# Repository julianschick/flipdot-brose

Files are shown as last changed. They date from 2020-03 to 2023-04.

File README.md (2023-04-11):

# flipdot-brose
Leiterplattenlayout für die Ansteuerung von Brose-Flipdotmodulen.

## Teileliste

Mit passenden Artikelbezeichnungen für den Berliner Elektroteilehändler [Segor](https://www.segor.de).

Anzahl | Beschreibung | Segor-Artikelbezeichnung
--|--|--
2 | Hohlsteckerbuchse für Printmontage 2,1/5,5mm | *DCBU 2,1-PRNB*
3 | Miniatursicherungshalter Littelfuse RM 5,08mm | *RSI-Halter/LP*
3 | Rundsicherungen träge (1A, 4A, 5A) | *RSI 1,0 A T*; *RSI 4,0 A T*; *RSI 5,0 A T*
1 | JST VH-Buchse 3-polig 90° | *B3PS-VH*
1 | Diode mind. 2A und 30V | *1N 5062*
1 | Diode mind. 6A und 5V | *P 600 M*
1 | Keramikkondensator 100n RM 2,5mm | *u10-R2.5-X7R*
1 | Elektrolytkondensator 10u RM 2,5mm | *ELRA 10u-50/105°/6,3x7*
1 | Linearregler 3.3V min. 500mA Formfaktor TO220 | *LD 1117 V33* 
6 | Shift-Register 8Bit 74HC595 | *74HC 595 N*
1 | Octal-Transceiver 76HC245 | *74HC 245 N*
4 | NPN-Darlington-Array 8 Bit ULN2803A | *ULN 2803 A*
2 | High-Side-Driver TD62783 (oder UDN2981) | *TD62783 APG*
8 | Widerstand 10K RM 5,08mm |
1 | ESP32-Development-Board NodeMCU/DEVKITV1 (15 Pole je Reihe und VCC- und GND-Pin nebeneinander)
1 | Wannenstecker 60-polig (2x30) RM 2,54mm mit (oder ohne) Niederhalter
1 | Pinheader 10-polig (2x5) RM 2,54mm (und passende Kurzschlussbrücken dazu)
2 | Pinheader 16-polig RM 2,54mm (eigentlich 15-polig)

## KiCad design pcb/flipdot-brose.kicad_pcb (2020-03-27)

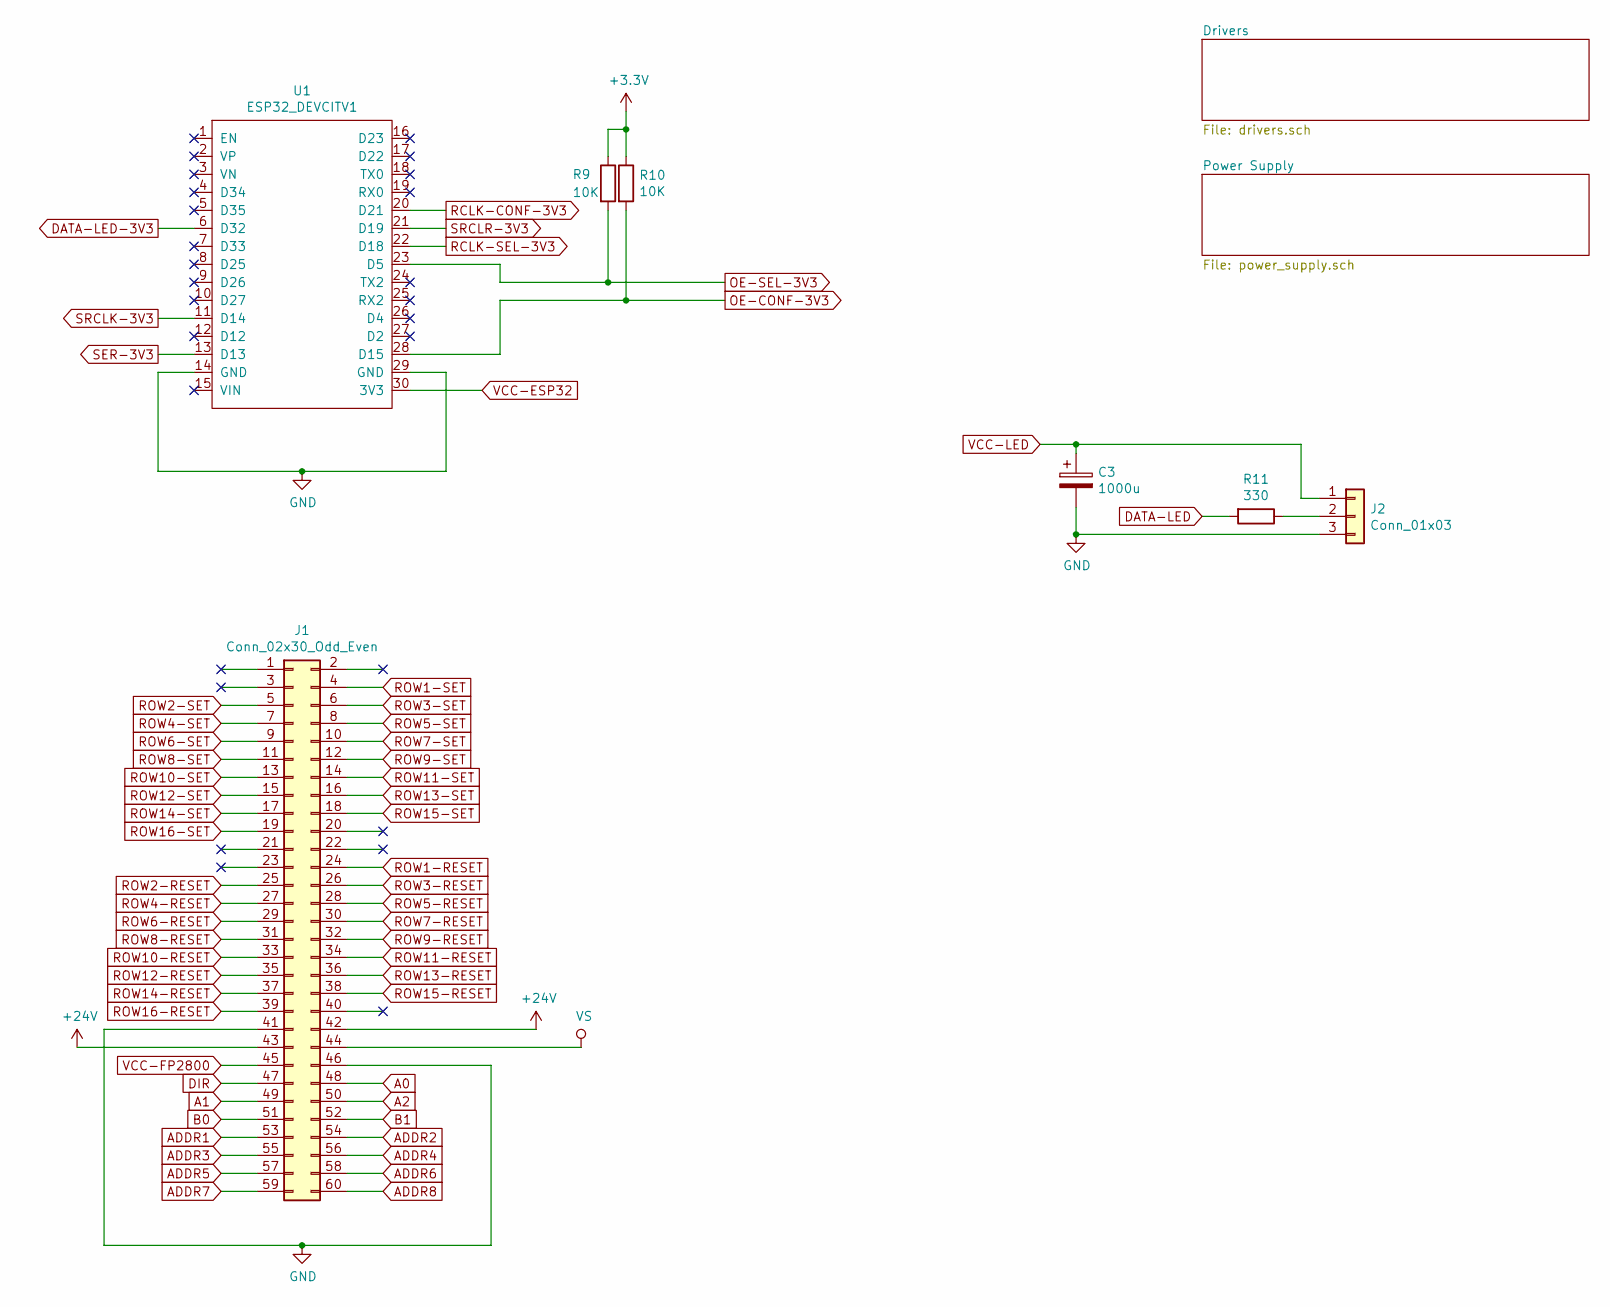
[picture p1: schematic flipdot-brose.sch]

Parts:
C3: 1000u; CP_Radial_D10.0mm_P5.00mm
J1: Conn_02x30_Odd_Even; IDC-Header_2x30_P2.54mm_Vertical_Lock
J2: Conn_01x03; JST_VH_B3PS-VH_2x3x3.96mm_Horizontal
R9, R10: 10K; R_Axial_DIN0204_L3.6mm_D1.6mm_P5.08mm_Horizontal
R11: 330; R_Axial_DIN0204_L3.6mm_D1.6mm_P5.08mm_Horizontal
U1: ESP32_DEVCITV1; ESP32_DEVKITV1

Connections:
+3V3: R9.1, R10.1; also elsewhere on the board
+24V: J1.42, J1.43; also elsewhere on the board
A0: J1.48; also elsewhere on the board
A1: J1.49; also elsewhere on the board
A2: J1.50; also elsewhere on the board
ADDR1: J1.53; also elsewhere on the board
ADDR2: J1.54; also elsewhere on the board
ADDR3: J1.55; also elsewhere on the board
ADDR4: J1.56; also elsewhere on the board
ADDR5: J1.57; also elsewhere on the board
ADDR6: J1.58; also elsewhere on the board
ADDR7: J1.59; also elsewhere on the board
ADDR8: J1.60; also elsewhere on the board
B0: J1.51; also elsewhere on the board
B1: J1.52; also elsewhere on the board
DATA-LED: R11.2; also elsewhere on the board
DATA-LED-3V3: U1.6 (D32); also elsewhere on the board
DIR: J1.47; also elsewhere on the board
GND: C3.2, J1.41, J1.46, J2.3, U1.14 (GND), U1.29 (GND); also elsewhere on the board
unnamed: J2.2, R11.1
OE-CONF-3V3: R10.2, U1.28 (D15); also elsewhere on the board
OE-SEL-3V3: R9.2, U1.23 (D5); also elsewhere on the board
RCLK-CONF-3V3: U1.20 (D21); also elsewhere on the board
RCLK-SEL-3V3: U1.22 (D18); also elsewhere on the board
ROW1-RESET: J1.24; also elsewhere on the board
ROW1-SET: J1.4; also elsewhere on the board
ROW2-RESET: J1.25; also elsewhere on the board
ROW2-SET: J1.5; also elsewhere on the board
ROW3-RESET: J1.26; also elsewhere on the board
ROW3-SET: J1.6; also elsewhere on the board
ROW4-RESET: J1.27; also elsewhere on the board
ROW4-SET: J1.7; also elsewhere on the board
ROW5-RESET: J1.28; also elsewhere on the board
ROW5-SET: J1.8; also elsewhere on the board
ROW6-RESET: J1.29; also elsewhere on the board
ROW6-SET: J1.9; also elsewhere on the board
ROW7-RESET: J1.30; also elsewhere on the board
ROW7-SET: J1.10; also elsewhere on the board
ROW8-RESET: J1.31; also elsewhere on the board
ROW8-SET: J1.11; also elsewhere on the board
ROW9-RESET: J1.32; also elsewhere on the board
ROW9-SET: J1.12; also elsewhere on the board
ROW10-RESET: J1.33; also elsewhere on the board
ROW10-SET: J1.13; also elsewhere on the board
ROW11-RESET: J1.34; also elsewhere on the board
ROW11-SET: J1.14; also elsewhere on the board
ROW12-RESET: J1.35; also elsewhere on the board
ROW12-SET: J1.15; also elsewhere on the board
ROW13-RESET: J1.36; also elsewhere on the board
ROW13-SET: J1.16; also elsewhere on the board
ROW14-RESET: J1.37; also elsewhere on the board
ROW14-SET: J1.17; also elsewhere on the board
ROW15-RESET: J1.38; also elsewhere on the board
ROW15-SET: J1.18; also elsewhere on the board
ROW16-RESET: J1.39; also elsewhere on the board
ROW16-SET: J1.19; also elsewhere on the board
SER-3V3: U1.13 (D13); also elsewhere on the board
SRCLK-3V3: U1.11 (D14); also elsewhere on the board
SRCLR-3V3: U1.21 (D19); also elsewhere on the board
VCC-ESP32: U1.30 (3V3); also elsewhere on the board
VCC-FP2800: J1.45; also elsewhere on the board
VCC-LED: C3.1, J2.1; also elsewhere on the board
VS: J1.44; also elsewhere on the board

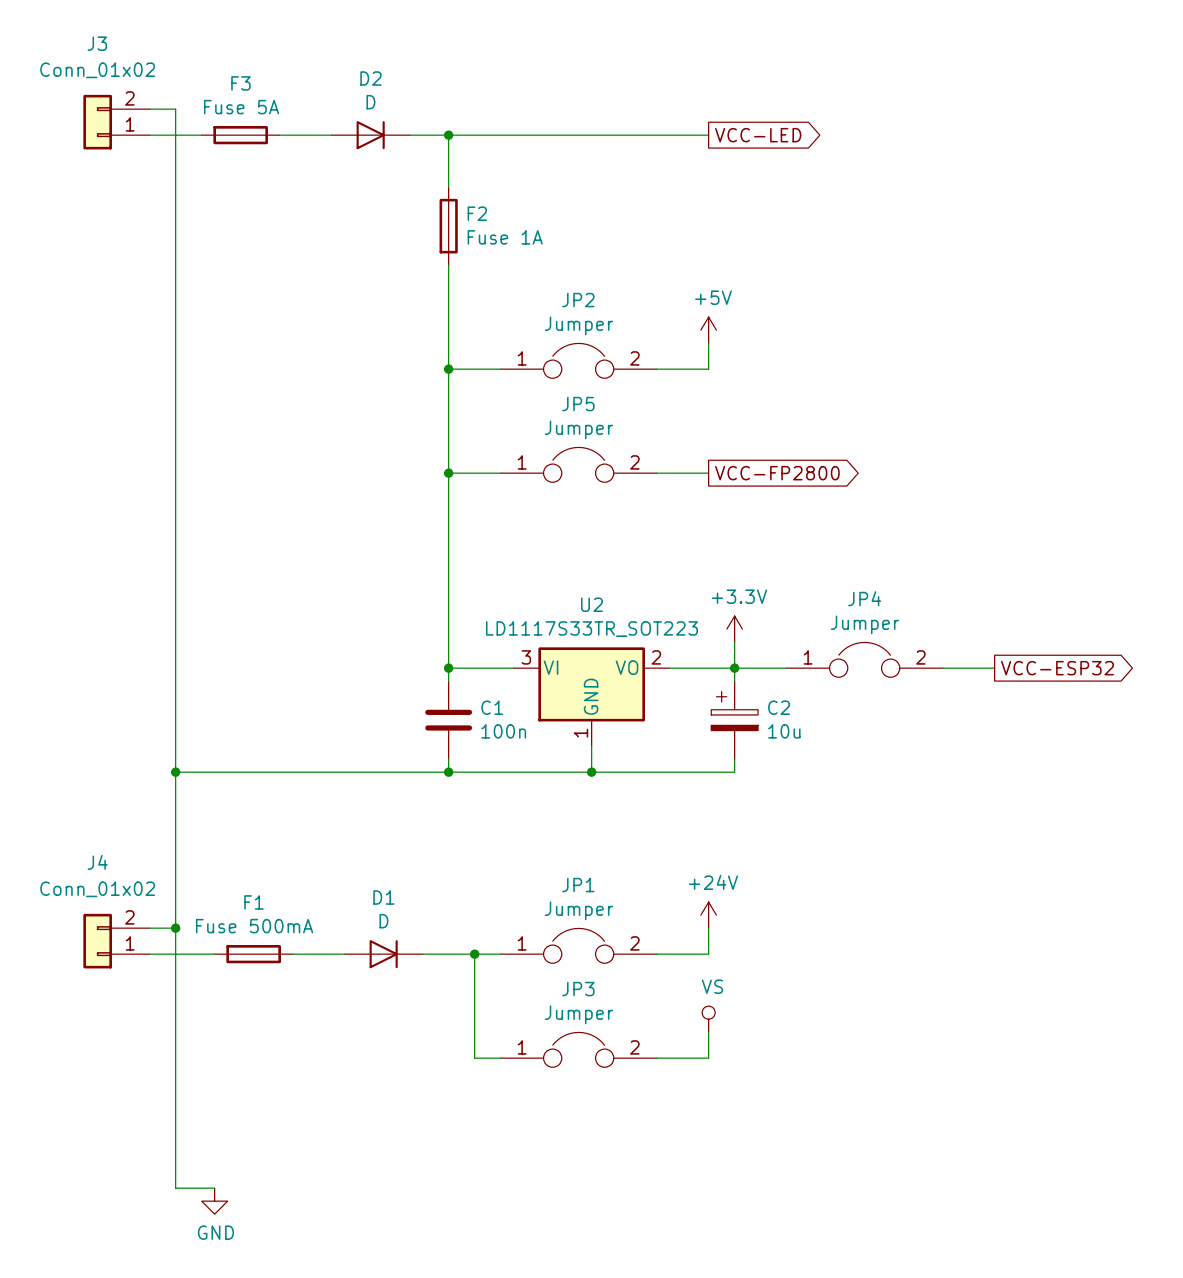
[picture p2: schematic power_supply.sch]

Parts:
C1: 100n; C_Disc_D5.0mm_W2.5mm_P2.50mm
C2: 10u; CP_Radial_D5.0mm_P2.50mm
D1: D; D_A-405_P7.62mm_Horizontal
D2: D; D_P600_R-6_P12.70mm_Horizontal
F1: Fuse 500mA; Fuseholder_Fuse_TR5_Littlefuse-No560_No460
F2: Fuse 1A; Fuseholder_Fuse_TR5_Littlefuse-No560_No460
F3: Fuse 5A; Fuseholder_Fuse_TR5_Littlefuse-No560_No460
J3, J4: Conn_01x02; TerminalBlock_MetzConnect_Type055_RT01502HDWU_Pitch5.00mm
JP1, JP2, JP3, JP4, JP5: Jumper; PinHeader_1x02_P2.54mm_Vertical
U2: LD1117S33TR_SOT223; TO-220-3_Horizontal

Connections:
+3V3: C2.1, JP4.1, U2.2 (VO); also elsewhere on the board
+5V: JP2.2; also elsewhere on the board
+24V: JP1.2; also elsewhere on the board
GND: C1.2, C2.2, J3.2, J4.2, U2.1 (GND); also elsewhere on the board
unnamed: C1.1, F2.2, JP2.1, JP5.1, U2.3 (VI)
unnamed: D1.1 (K), JP1.1, JP3.1
unnamed: D1.2 (A), F1.1
unnamed: D2.2 (A), F3.1
unnamed: F1.2, J4.1
unnamed: F3.2, J3.1
VCC-ESP32: JP4.2; also elsewhere on the board
VCC-FP2800: JP5.2; also elsewhere on the board
VCC-LED: D2.1 (K), F2.1; also elsewhere on the board
VS: JP3.2; also elsewhere on the board

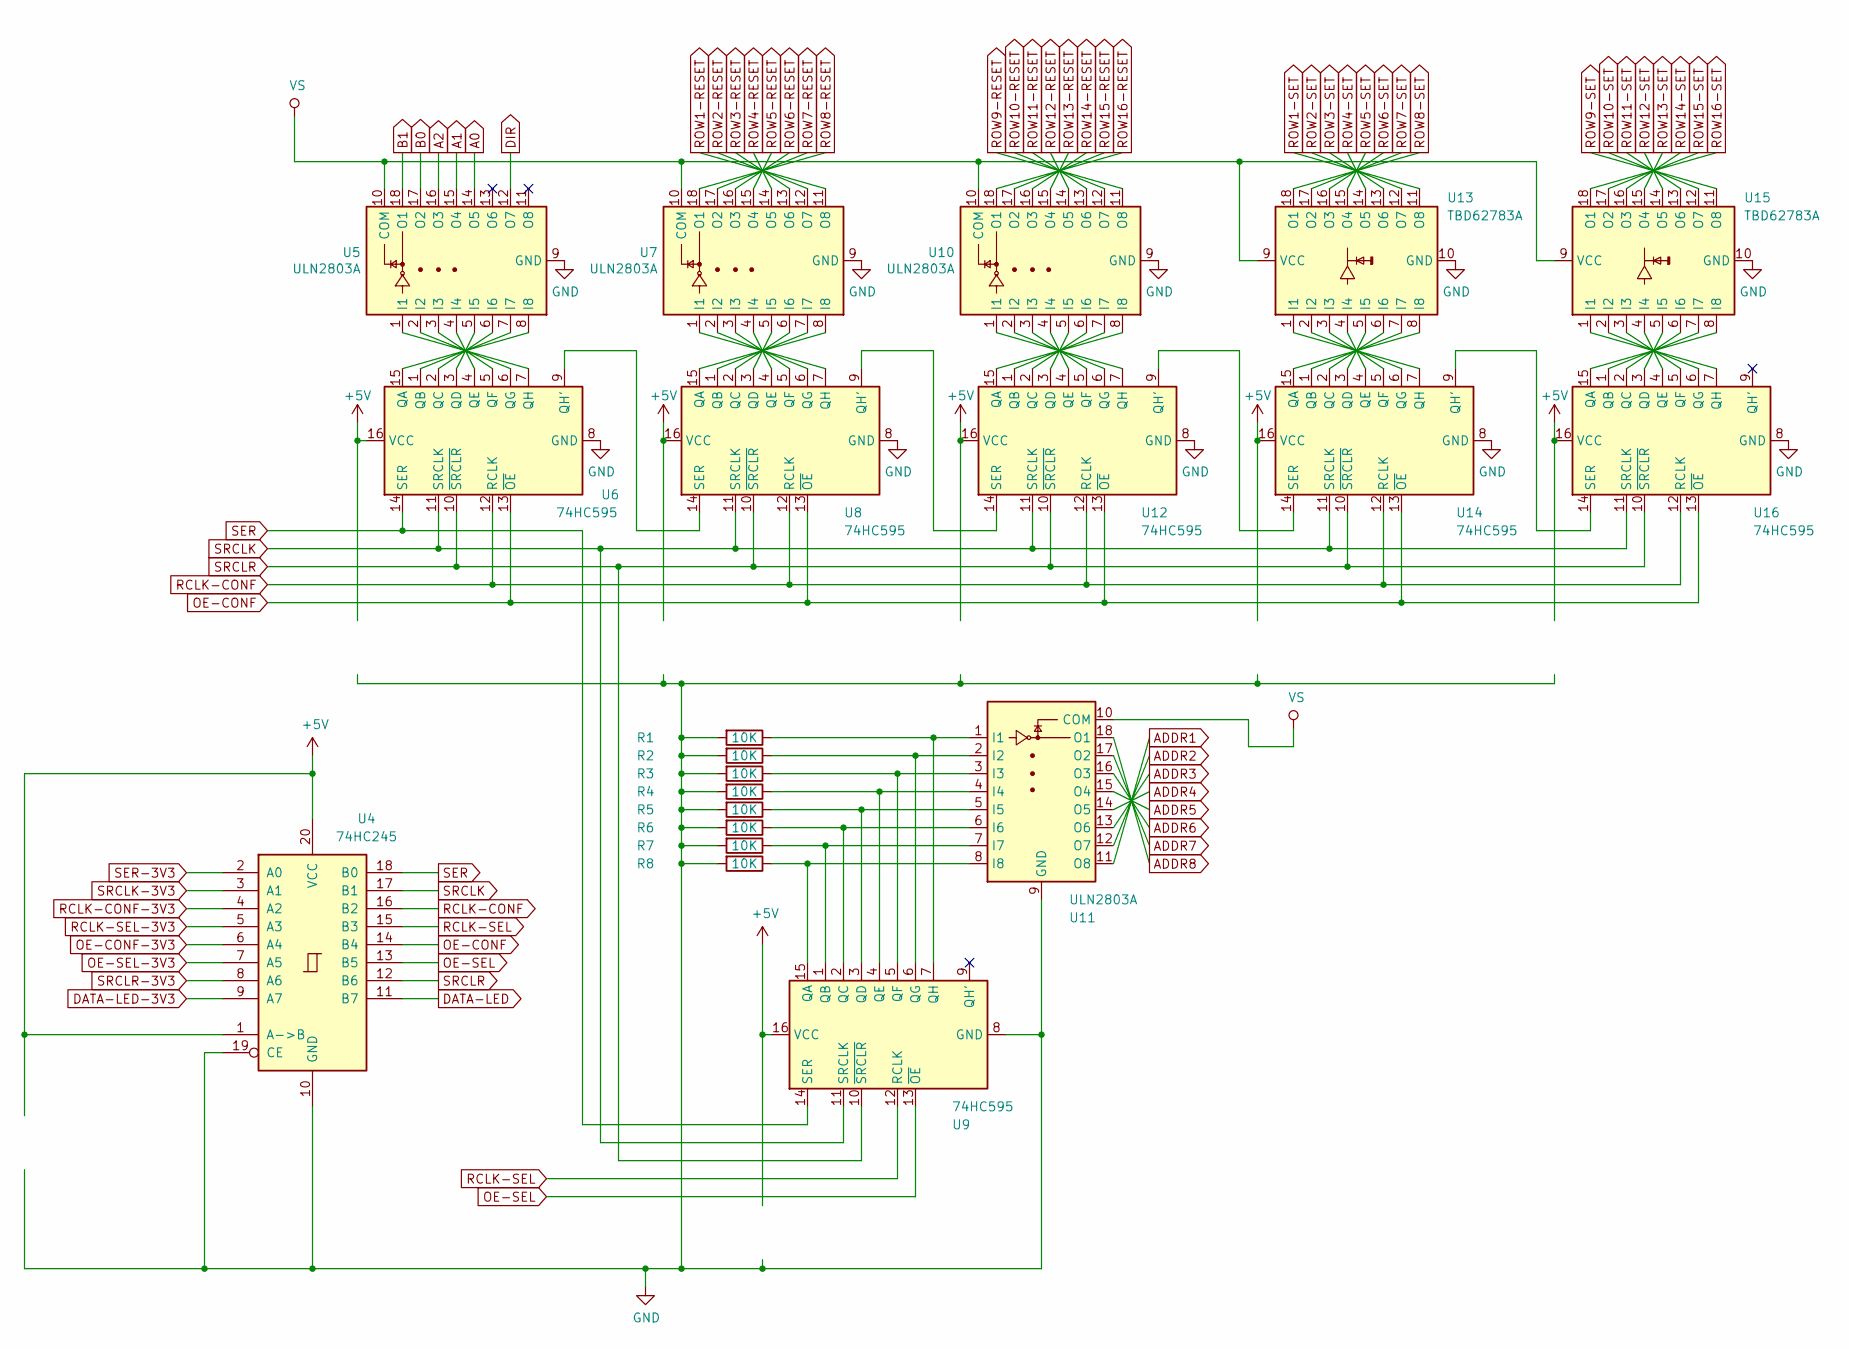
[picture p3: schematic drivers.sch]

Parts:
R1, R2, R3, R4, R5, R6, R7, R8: 10K; R_Axial_DIN0204_L3.6mm_D1.6mm_P5.08mm_Horizontal
U4: 74HC245; DIP-20_W7.62mm
U5, U7, U10, U11: ULN2803A; DIP-18_W7.62mm
U6, U8, U9, U12, U14, U16: 74HC595; DIP-16_W7.62mm
U13, U15: TBD62783A; DIP-18_W7.62mm

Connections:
+5V: U4.1 (A->B), U4.20 (VCC), U6.16 (VCC), U8.16 (VCC), U9.16 (VCC), U12.16 (VCC), U14.16 (VCC), U16.16 (VCC); also elsewhere on the board
A0: U5.14 (O5); also elsewhere on the board
A1: U5.15 (O4); also elsewhere on the board
A2: U5.16 (O3); also elsewhere on the board
ADDR1: U11.11 (O8); also elsewhere on the board
ADDR2: U11.12 (O7); also elsewhere on the board
ADDR3: U11.13 (O6); also elsewhere on the board
ADDR4: U11.14 (O5); also elsewhere on the board
ADDR5: U11.15 (O4); also elsewhere on the board
ADDR6: U11.16 (O3); also elsewhere on the board
ADDR7: U11.17 (O2); also elsewhere on the board
ADDR8: U11.18 (O1); also elsewhere on the board
B0: U5.17 (O2); also elsewhere on the board
B1: U5.18 (O1); also elsewhere on the board
DATA-LED: U4.11 (B7); also elsewhere on the board
DATA-LED-3V3: U4.9 (A7); also elsewhere on the board
DIR: U5.12 (O7); also elsewhere on the board
GND: R1.2, R2.2, R3.2, R4.2, R5.2, R6.2, R7.2, R8.2, U4.10 (GND), U4.19 (CE), U5.9 (GND), U6.8 (GND), U7.9 (GND), U8.8 (GND), U9.8 (GND), U10.9 (GND), U11.9 (GND), U12.8 (GND), U13.10 (GND), U14.8 (GND), U15.10 (GND), U16.8 (GND); also elsewhere on the board
unnamed: R1.1, U9.7 (QH), U11.1 (I1)
unnamed: R2.1, U9.6 (QG), U11.2 (I2)
unnamed: R3.1, U9.5 (QF), U11.3 (I3)
unnamed: R4.1, U9.4 (QE), U11.4 (I4)
unnamed: R5.1, U9.3 (QD), U11.5 (I5)
unnamed: R6.1, U9.2 (QC), U11.6 (I6)
unnamed: R7.1, U9.1 (QB), U11.7 (I7)
unnamed: R8.1, U9.15 (QA), U11.8 (I8)
unnamed: U5.1 (I1), U6.7 (QH)
unnamed: U5.2 (I2), U6.6 (QG)
unnamed: U5.3 (I3), U6.5 (QF)
unnamed: U5.4 (I4), U6.4 (QE)
unnamed: U5.5 (I5), U6.3 (QD)
unnamed: U5.6 (I6), U6.2 (QC)
unnamed: U5.7 (I7), U6.1 (QB)
unnamed: U5.8 (I8), U6.15 (QA)
unnamed: U6.9 (QH'), U8.14 (SER)
unnamed: U7.1 (I1), U8.7 (QH)
unnamed: U7.2 (I2), U8.6 (QG)
unnamed: U7.3 (I3), U8.5 (QF)
unnamed: U7.4 (I4), U8.4 (QE)
unnamed: U7.5 (I5), U8.3 (QD)
unnamed: U7.6 (I6), U8.2 (QC)
unnamed: U7.7 (I7), U8.1 (QB)
unnamed: U7.8 (I8), U8.15 (QA)
unnamed: U10.1 (I1), U12.7 (QH)
unnamed: U10.2 (I2), U12.6 (QG)
unnamed: U10.3 (I3), U12.5 (QF)
unnamed: U10.4 (I4), U12.4 (QE)
unnamed: U10.5 (I5), U12.3 (QD)
unnamed: U10.6 (I6), U12.2 (QC)
unnamed: U10.7 (I7), U12.1 (QB)
unnamed: U10.8 (I8), U12.15 (QA)
unnamed: U12.9 (QH'), U14.14 (SER)
unnamed: U8.9 (QH'), U12.14 (SER)
unnamed: U13.1 (I1), U14.7 (QH)
unnamed: U13.2 (I2), U14.6 (QG)
unnamed: U13.3 (I3), U14.5 (QF)
unnamed: U13.4 (I4), U14.4 (QE)
unnamed: U13.5 (I5), U14.3 (QD)
unnamed: U13.6 (I6), U14.2 (QC)
unnamed: U13.7 (I7), U14.1 (QB)
unnamed: U13.8 (I8), U14.15 (QA)
unnamed: U14.9 (QH'), U16.14 (SER)
unnamed: U15.1 (I1), U16.7 (QH)
unnamed: U15.2 (I2), U16.6 (QG)
unnamed: U15.3 (I3), U16.5 (QF)
unnamed: U15.4 (I4), U16.4 (QE)
unnamed: U15.5 (I5), U16.3 (QD)
unnamed: U15.6 (I6), U16.2 (QC)
unnamed: U15.7 (I7), U16.1 (QB)
unnamed: U15.8 (I8), U16.15 (QA)
OE-CONF: U4.14 (B4), U6.13 (~OE), U8.13 (~OE), U12.13 (~OE), U14.13 (~OE), U16.13 (~OE)
OE-CONF-3V3: U4.6 (A4); also elsewhere on the board
OE-SEL: U4.13 (B5), U9.13 (~OE)
OE-SEL-3V3: U4.7 (A5); also elsewhere on the board
RCLK-CONF: U4.16 (B2), U6.12 (RCLK), U8.12 (RCLK), U12.12 (RCLK), U14.12 (RCLK), U16.12 (RCLK)
RCLK-CONF-3V3: U4.4 (A2); also elsewhere on the board
RCLK-SEL: U4.15 (B3), U9.12 (RCLK)
RCLK-SEL-3V3: U4.5 (A3); also elsewhere on the board
ROW1-RESET: U7.11 (O8); also elsewhere on the board
ROW1-SET: U13.11 (O8); also elsewhere on the board
ROW2-RESET: U7.12 (O7); also elsewhere on the board
ROW2-SET: U13.12 (O7); also elsewhere on the board
ROW3-RESET: U7.13 (O6); also elsewhere on the board
ROW3-SET: U13.13 (O6); also elsewhere on the board
ROW4-RESET: U7.14 (O5); also elsewhere on the board
ROW4-SET: U13.14 (O5); also elsewhere on the board
ROW5-RESET: U7.15 (O4); also elsewhere on the board
ROW5-SET: U13.15 (O4); also elsewhere on the board
ROW6-RESET: U7.16 (O3); also elsewhere on the board
ROW6-SET: U13.16 (O3); also elsewhere on the board
ROW7-RESET: U7.17 (O2); also elsewhere on the board
ROW7-SET: U13.17 (O2); also elsewhere on the board
ROW8-RESET: U7.18 (O1); also elsewhere on the board
ROW8-SET: U13.18 (O1); also elsewhere on the board
ROW9-RESET: U10.11 (O8); also elsewhere on the board
ROW9-SET: U15.11 (O8); also elsewhere on the board
ROW10-RESET: U10.12 (O7); also elsewhere on the board
ROW10-SET: U15.12 (O7); also elsewhere on the board
ROW11-RESET: U10.13 (O6); also elsewhere on the board
ROW11-SET: U15.13 (O6); also elsewhere on the board
ROW12-RESET: U10.14 (O5); also elsewhere on the board
ROW12-SET: U15.14 (O5); also elsewhere on the board
ROW13-RESET: U10.15 (O4); also elsewhere on the board
ROW13-SET: U15.15 (O4); also elsewhere on the board
ROW14-RESET: U10.16 (O3); also elsewhere on the board
ROW14-SET: U15.16 (O3); also elsewhere on the board
ROW15-RESET: U10.17 (O2); also elsewhere on the board
ROW15-SET: U15.17 (O2); also elsewhere on the board
ROW16-RESET: U10.18 (O1); also elsewhere on the board
ROW16-SET: U15.18 (O1); also elsewhere on the board
SER: U4.18 (B0), U6.14 (SER), U9.14 (SER)
SER-3V3: U4.2 (A0); also elsewhere on the board
SRCLK: U4.17 (B1), U6.11 (SRCLK), U8.11 (SRCLK), U9.11 (SRCLK), U12.11 (SRCLK), U14.11 (SRCLK), U16.11 (SRCLK)
SRCLK-3V3: U4.3 (A1); also elsewhere on the board
SRCLR: U4.12 (B6), U6.10 (~SRCLR), U8.10 (~SRCLR), U9.10 (~SRCLR), U12.10 (~SRCLR), U14.10 (~SRCLR), U16.10 (~SRCLR)
SRCLR-3V3: U4.8 (A6); also elsewhere on the board
VS: U5.10 (COM), U7.10 (COM), U10.10 (COM), U11.10 (COM), U13.9 (VCC), U15.9 (VCC); also elsewhere on the board

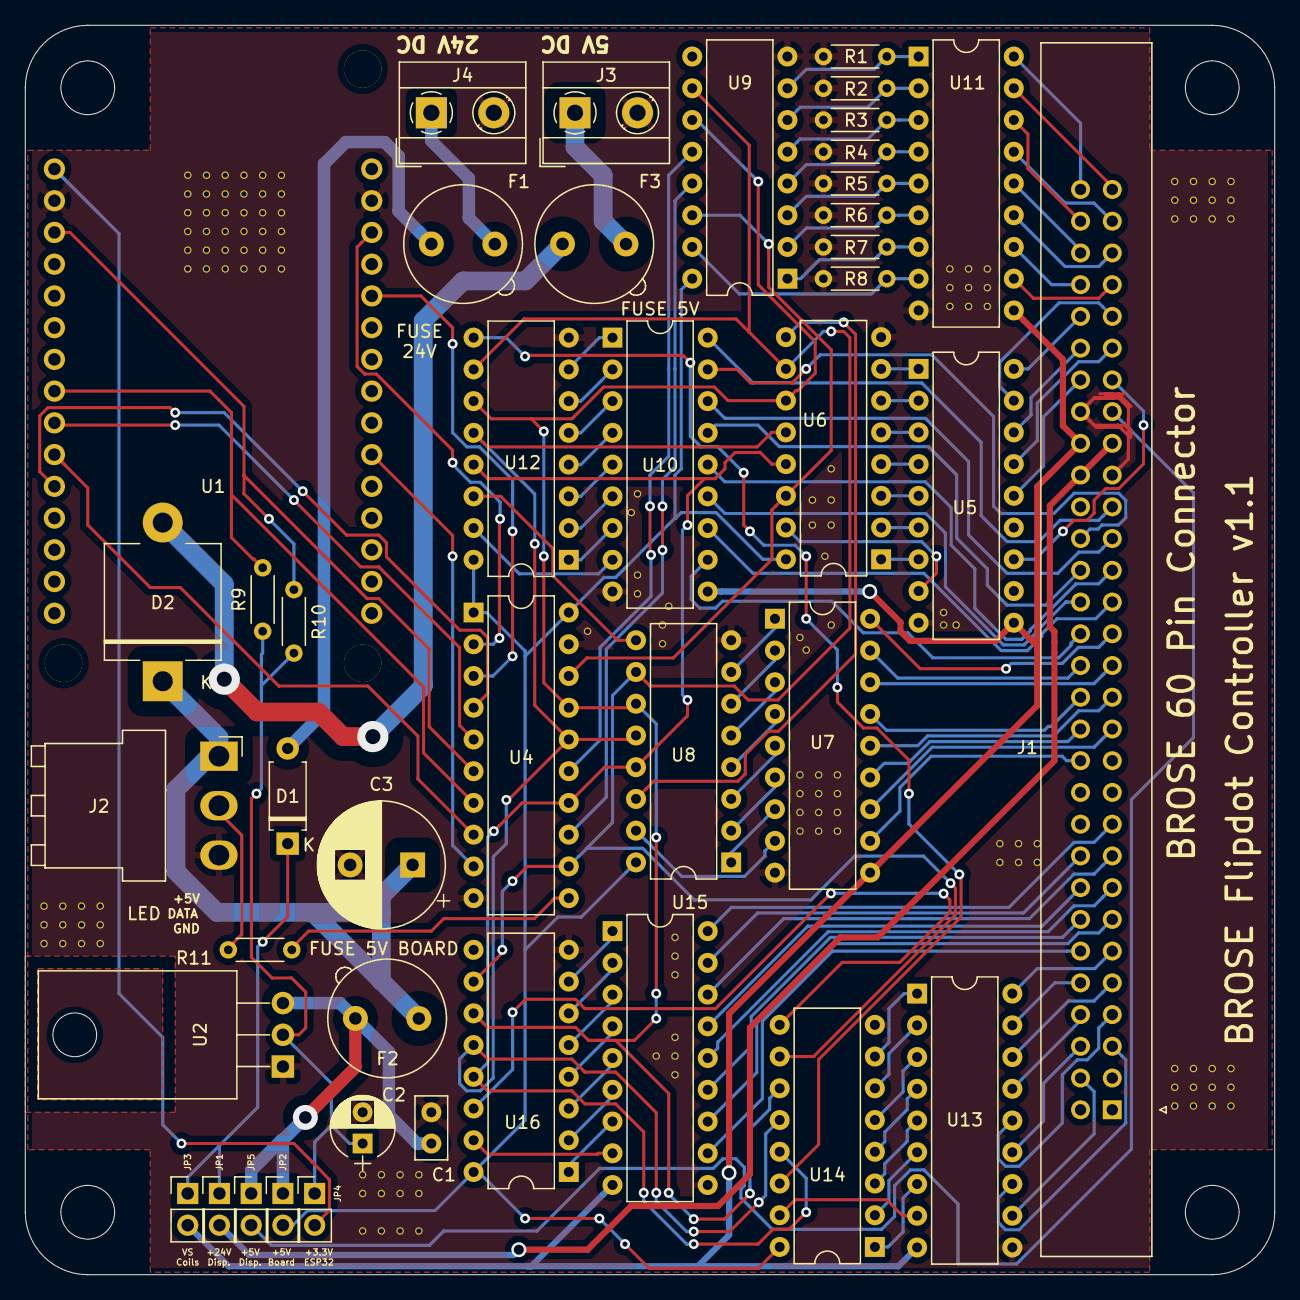
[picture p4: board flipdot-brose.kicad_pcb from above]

Board: 2 copper layers, 100.0 x 100.0 mm, 43 parts (0 on the bottom side), 129 nets.

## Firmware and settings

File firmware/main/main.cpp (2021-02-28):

#include "libs/nvs.h"
#include "libs/blue.h"
#include "libs/mdns.h"
#include "libs/wifi.h"
#include "libs/tcp_server.h"

#define PIN_NUM_MOSI GPIO_NUM_13
#define PIN_NUM_CLK  GPIO_NUM_14

#define PIN_NUM_CLR GPIO_NUM_19
#define PIN_NUM_RCLK_SEL GPIO_NUM_18
#define PIN_NUM_RCLK_CONF GPIO_NUM_21
#define PIN_NUM_OE_SEL GPIO_NUM_5
#define PIN_NUM_OE_CONF GPIO_NUM_15

#define TAG "startup"
#define LOG_LOCAL_LEVEL ESP_LOG_INFO
#include <esp_log.h>

WS2812Controller* led_ctrl;
WS2812Buffer* ledBuffer;
FlipdotBuffer* flipdotBuffer;

TaskHandle_t ledTask;
TaskHandle_t tcpServerTask;
TaskHandle_t flipdotTask;

inline void safety_init() {
    gpio_config_t io_conf;
    io_conf.intr_type = GPIO_INTR_DISABLE;
    io_conf.mode = GPIO_MODE_OUTPUT;
    io_conf.pin_bit_mask = (uint64_t) 1 << (uint64_t) PIN_NUM_OE_CONF;;
    io_conf.pull_down_en = GPIO_PULLDOWN_DISABLE;
    io_conf.pull_up_en = GPIO_PULLUP_DISABLE;
    gpio_config(&io_conf);
    gpio_set_level(PIN_NUM_OE_CONF, 1);
}

void led_task(void* params) {

    led_ctrl->readState();
    TickType_t lastStateSave = xTaskGetTickCount();

    while(1) {

        ledBuffer->executeNext(1000);

        if ((xTaskGetTickCount() - lastStateSave)*portTICK_PERIOD_MS > 20*1000) {
            if (led_ctrl->saveStateIfNecessary()) {
                lastStateSave = xTaskGetTickCount();
            }
        }
    }

}

void flipdot_task(void* params) {
    while(1) {
        flipdotBuffer->executeNext(1000);
    }
}

extern "C" void app_main() {

    gpio_set_level(PIN_NUM_OE_CONF, 1);
    safety_init();

    ESP_LOGI(TAG, "Safety init done");

    flipdot_driver_pins_t pins;
    pins.ser = PIN_NUM_MOSI;
    pins.serclk = PIN_NUM_CLK;
    pins.clr = PIN_NUM_CLR;
    pins.rclk_conf = PIN_NUM_RCLK_CONF;
    pins.rclk_sel = PIN_NUM_RCLK_SEL;
    pins.oe_conf = PIN_NUM_OE_CONF;
    pins.oe_sel = PIN_NUM_OE_SEL;

    flipdot_driver_timing_config_t timing;
    timing.set_usecs = 200;
    timing.reset_usecs = 200;

    FlipdotDriver *drv = new FlipdotDriver(28, 16, 4, &pins, &timing);
    ESP_LOGI(TAG, "Flipdot driver initialized");

    uint32_t short_period = 28;
    uint32_t long_period = 72;
    ws2812_timing_config_t timing_config = {short_period, long_period, long_period, short_period};
    WS2812Driver* led_drv = new WS2812Driver(GPIO_NUM_32, RMT_CHANNEL_0, timing_config, 36);
    ESP_LOGI(TAG, "LED driver initialized");

    FlipdotDisplay* dsp = new FlipdotDisplay(drv);
    led_ctrl = new WS2812Controller(led_drv);
    led_drv->clear();
    ledBuffer = new WS2812Buffer(led_ctrl, 10);
    flipdotBuffer = new FlipdotBuffer(dsp, 10);
    ESP_LOGI(TAG, "Controllers initialized");

    Nvs::setup();

    // general networking pre-setup (main work is done in Wifi::setup())
    ESP_ERROR_CHECK(esp_netif_init());
    ESP_ERROR_CHECK(esp_event_loop_create_default());
    start_mdns_service();
    Wifi::setup();
    Blue::setup();

    ESP_LOGI(TAG, "Network services up");

    ESP_LOGI(TAG, "Starting TCP server task...");
    xTaskCreatePinnedToCore(tcp_server_task, "tcp-server-task", 2600, NULL, configMAX_PRIORITIES - 2, &tcpServerTask, 0);

    ESP_LOGI(TAG, "Starting LED task...");
    xTaskCreatePinnedToCore(led_task, "led-task", 1800, NULL, configMAX_PRIORITIES - 1, &ledTask, 0);

    ESP_LOGI(TAG, "Starting flipdot task...");
    xTaskCreatePinnedToCore(flipdot_task, "flipdot-task", 2000, NULL, configMAX_PRIORITIES - 1, &flipdotTask, 1);

    ESP_LOGI(TAG, "Init sequence done");
}

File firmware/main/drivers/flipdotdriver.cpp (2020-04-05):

#include "flipdotdriver.h"

#include <algorithm> //std::min/std::max

FlipdotDriver::FlipdotDriver(int module_width_, int module_height_, int device_count_,
        flipdot_driver_pins_t* pins_,
        flipdot_driver_timing_config_t* timing_) :
    module_width(module_width_), module_height(module_height_), device_count(device_count_)
{
    pins = *pins_;
    timing = *timing_;
    bound_timing();

    total_width = module_width * device_count;
    total_height = module_height;

    init_gpio();
    init_spi();

    // Activate config register output, can now operate
    gpio_set_level(pins.oe_conf, 0);
}

void FlipdotDriver::init_spi() {
    esp_err_t ret;

    spi_bus_config_t bus_config;
    bus_config.miso_io_num = -1;
    bus_config.mosi_io_num = pins.ser;
    bus_config.sclk_io_num = pins.serclk;
    bus_config.quadwp_io_num = -1;
    bus_config.quadhd_io_num = -1;
    bus_config.max_transfer_sz = 0;
    bus_config.flags = SPICOMMON_BUSFLAG_MASTER;
    bus_config.intr_flags = 0;

    spi_device_interface_config_t device_config;
    device_config.command_bits = 0;
    device_config.address_bits = 0;
    device_config.dummy_bits = 0;
    device_config.mode=0;
    device_config.duty_cycle_pos = 128; // 50%/50%
    device_config.cs_ena_pretrans = 0;
    device_config.cs_ena_posttrans = 0;
    device_config.clock_speed_hz=APB_CLK_FREQ / 2; // 40 MHz (max Speed for 74HC595)
    device_config.input_delay_ns = 0;
    device_config.spics_io_num=-1;
    device_config.flags = 0;
    device_config.queue_size=1;
    device_config.pre_cb = 0;
    device_config.post_cb = 0;

    ret = spi_bus_initialize(HSPI_HOST, &bus_config, 1);
    ESP_ERROR_CHECK(ret);
    ret = spi_bus_add_device(HSPI_HOST, &device_config, &spi);
    ESP_ERROR_CHECK(ret);

}

void FlipdotDriver::init_gpio() {
    uint64_t mask = 0x00;
    mask |= (uint64_t) 0x01 << (uint64_t) pins.clr;
    mask |= (uint64_t) 0x01 << (uint64_t) pins.rclk_sel;
    mask |= (uint64_t) 0x01 << (uint64_t) pins.rclk_conf;
    mask |= (uint64_t) 0x01 << (uint64_t) pins.oe_sel;
    mask |= (uint64_t) 0x01 << (uint64_t) pins.oe_conf;

    gpio_config_t io_conf;
    io_conf.intr_type = GPIO_INTR_DISABLE;
    io_conf.mode = GPIO_MODE_OUTPUT;
    io_conf.pin_bit_mask = mask;
    io_conf.pull_down_en = GPIO_PULLDOWN_DISABLE;
    io_conf.pull_up_en = GPIO_PULLUP_DISABLE;
    ESP_ERROR_CHECK(gpio_config(&io_conf));

    // Disable config and select outputs
    gpio_set_level(pins.oe_conf, 1);
    gpio_set_level(pins.oe_sel, 1);

    // Disable clear flag
    gpio_set_level(pins.clr, 1);

    // RCLK lines on HIGH by default
    gpio_set_level(pins.rclk_sel, 1);
    gpio_set_level(pins.rclk_conf, 1);

    // Zero all shift-registers
    clear_registers();

    // ... which means no device is selected
    selected_device = 0;
}

void FlipdotDriver::flip(PixelCoord& coord, bool show) {
    flip(coord.x, coord.y, show);
}

void FlipdotDriver::flip(int x, int y, bool show) {
    if (x < 0 || x >= total_width) return;
    if (y < 0 || y >= total_height) return;

    int device = (x / module_width) + 1;
    int device_x = x % module_width;

    if (selected_device != device) {
        select_device(device);
    }

    uint16_t row_mask = encode_row(y);
    uint8_t buffer[5];

    // set
    if (show) {
        buffer[0] = (uint8_t) (row_mask >> 8);
        buffer[1] = (uint8_t) row_mask;
        buffer[2] = 0x00;
        buffer[3] = 0x00;
        buffer[4] = encode_status(device_x, 0);

    // reset
    } else {
        buffer[0] = 0x00;
        buffer[1] = 0x00;
        buffer[2] = (uint8_t) (row_mask >> 8);
        buffer[3] = (uint8_t) row_mask;
        buffer[4] = encode_status(device_x, 1);
    }

    spi_transaction_t tx;
    tx.flags = 0;
    tx.cmd = 0;
    tx.addr = 0;
    tx.length = 5 * 8;
    tx.rxlength = 0;
    tx.rx_buffer = 0;
    tx.tx_buffer = buffer;

    gpio_set_level(pins.rclk_conf, 0);
    ESP_ERROR_CHECK(spi_device_transmit(spi, &tx));
    gpio_set_level(pins.rclk_conf, 1);

    ets_delay_us(1);
    gpio_set_level(pins.oe_sel, 0);
    ets_delay_us(show ? timing.set_usecs : timing.reset_usecs);
    gpio_set_level(pins.oe_sel, 1);
}

void FlipdotDriver::select_device(int device) {
    uint8_t mask = 0x01;
    mask <<= (device - 1);

    spi_transaction_t tx;
    tx.flags = 0;
    tx.cmd = 0;
    tx.addr = 0;
    tx.length = 8;
    tx.rxlength = 0;
    tx.rx_buffer = 0;
    tx.tx_buffer = &mask;

    gpio_set_level(pins.rclk_sel, 0);
    ESP_ERROR_CHECK(spi_device_transmit(spi, &tx));
    gpio_set_level(pins.rclk_sel, 1);

    selected_device = device;
}

uint8_t FlipdotDriver::encode_column(int x) {
    if (x < 0 || x >= module_width) return 0x00;

    int col = x + 1;
    if (col <= 7) return col;
    if (col <= 14) return col + 1;
    if (col <= 21) return col + 2;
    return col + 3;
}

uint8_t FlipdotDriver::encode_status(int x, int dir) {
    uint8_t result = ~encode_column(x) << 3;
    if (dir == 0) {
        result |= BIT1;
    }
    return result;
}

uint16_t FlipdotDriver::encode_row(int y) {
    if (y < 0 || y >= module_height) {
        return 0x0000;
    }
    return 0x0001 << y;
}

void FlipdotDriver::clear_registers() {
    gpio_set_level(pins.clr, 0);

    gpio_set_level(pins.rclk_conf, 0);
    gpio_set_level(pins.rclk_sel, 0);

    ets_delay_us(1);

    gpio_set_level(pins.rclk_conf, 1);
    gpio_set_level(pins.rclk_sel, 1);

    gpio_set_level(pins.clr, 1);
}

void FlipdotDriver::set_timing(int usecs) {
    timing.set_usecs = usecs;
    timing.reset_usecs = usecs;
    bound_timing();
}

void FlipdotDriver::bound_timing() {
    timing.set_usecs = std::min(timing.set_usecs, 1000);
    timing.set_usecs = std::max(timing.set_usecs, 0);
    timing.reset_usecs = std::min(timing.reset_usecs, 1000);
    timing.reset_usecs = std::max(timing.reset_usecs, 0);
}

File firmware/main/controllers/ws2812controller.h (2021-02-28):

#ifndef WS2812CONTROLLER_H
#define WS2812CONTROLLER_H

#include <vector>
#include <freertos/FreeRTOS.h>
#include <freertos/semphr.h>
#include "../drivers/ws2812driver.h"

class WS2812Controller {

public:

    struct LedChangeCommand {
        size_t addr;
        color_t color;
    };

    enum TransitionMode {
        IMMEDIATE           = 0x01,
        LINEAR_SLOW         = 0x02,
        LINEAR_MEDIUM       = 0x03,
        LINEAR_QUICK        = 0x04,
        SLIDE_SLOW          = 0x05,
        SLIDE_MEDIUM        = 0x06,
        SLIDE_QUICK         = 0x07
    };

    WS2812Controller(WS2812Driver* drv);
    ~WS2812Controller();

    void setTransitionMode(TransitionMode mode);
    void setAllLedsToSameColor(color_t color);
    void setLeds(std::vector<LedChangeCommand> *changes);

public:
    size_t getLedCount() { return n; };
    color_t* getAll();
    TransitionMode getTransitionMode() { return transitionMode; };

    bool saveStateIfNecessary();
    void saveState();
    void readState();

    inline void setMutex(SemaphoreHandle_t m) { mutex = m; };
    inline void lock() {
        if (mutex != nullptr) {
            xSemaphoreTake(mutex, portMAX_DELAY);
        }
    }
    inline void unlock() {
        if (mutex != nullptr) {
            xSemaphoreGive(mutex);
        }
    }

private:
    WS2812Driver* drv;
    SemaphoreHandle_t mutex = nullptr;

    size_t n;
    color_t* state;

    TransitionMode transitionMode;
    color_t* startState;
    color_t* endState;
    int64_t lastCycle = 0;

    // for nvs storage
    bool newState = false;
    bool loadingFromNvs = false;

    // in milliseconds
    static const uint32_t LINEAR_SLOW_DELAY = 50;
    static const uint32_t LINEAR_MEDIUM_DELAY = 25;
    static const uint32_t LINEAR_QUICK_DELAY = 5;

    static const uint32_t SLIDE_SLOW_DELAY = 50;
    static const uint32_t SLIDE_MEDIUM_DELAY = 25;
    static const uint32_t SLIDE_QUICK_DELAY = 5;

    static int getDelayByMode(TransitionMode mode) {
        switch(mode) {
            case LINEAR_SLOW: return LINEAR_SLOW_DELAY;
            case LINEAR_MEDIUM: return LINEAR_MEDIUM_DELAY;
            case LINEAR_QUICK: return LINEAR_QUICK_DELAY;
            case SLIDE_SLOW: return SLIDE_SLOW_DELAY;
            case SLIDE_MEDIUM: return SLIDE_MEDIUM_DELAY;
            case SLIDE_QUICK: return SLIDE_QUICK_DELAY;
            default: return 0;
        }
    };

    void transition();
    void copy(color_t* dest, color_t* src);

};


#endif //WS2812CONTROLLER_H

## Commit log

2019-12-24 ws2812driver + partitions
    [partitions.csv]
2020-01-05 bitarray, led-driver, http-server
2020-02-26 pcb and firmware repo merge
    [drivers.sch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]
2020-03-17 command interpreter
    [partitions.csv]
2020-03-27 resistor/capacitor for leds
    [flipdot-brose.kicad_pcb, flipdot-brose.sch]
2020-03-29 buffered led driver
2020-04-05 led slide, restructure
2020-04-27 some getters and bugfixes
    [commandinterpreter.cpp, main.cpp, ws2812buffer.cpp]
2021-03-14 pixelfont utf and canvas
    [tcp_chart.ods]
2021-04-17 new command 'Scroll'
    [tcp_chart.ods]
2024-11-16 opened with newer kicad-version
